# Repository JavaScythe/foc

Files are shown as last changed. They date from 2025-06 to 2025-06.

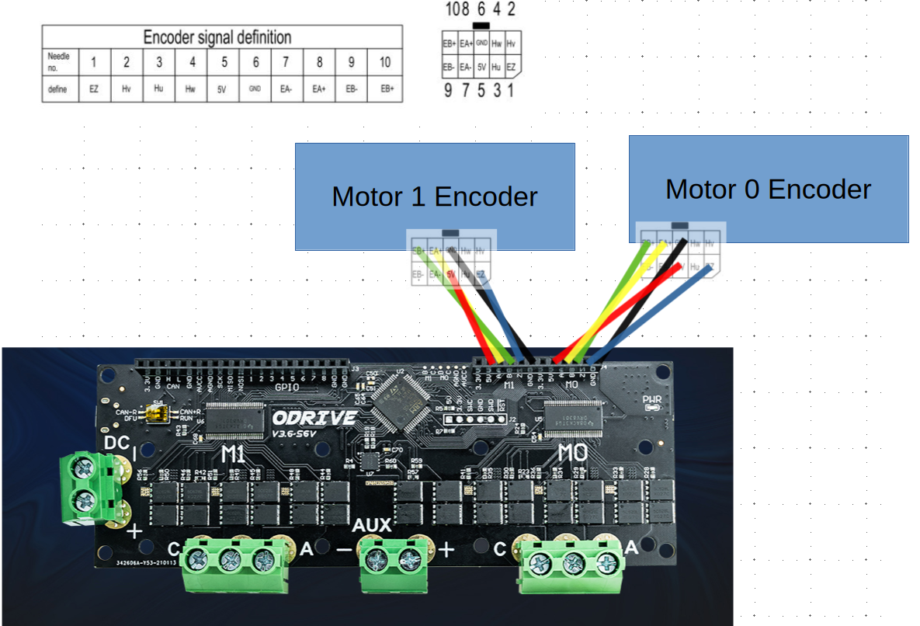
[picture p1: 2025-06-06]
motorencoderwiringguide.png

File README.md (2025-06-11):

# foc
Hyper realistic two-channel sim racing seatbelt tensioner with two 48V 54+54A FOC motors and controller that blows commercial 1300$ solutions out of the water

Specifically, it is high torque low latency that comes with its own software with support for real dynamic frequency effects for haptic feedback

### PLEASE see [JOURNAL.md](JOURNAL.md)

### Why?
- HackClub's great initiative [highway](https://highway.hackclub.com): not just "free money" but a nice community of beginners and advanced that help each other
- Lack of respect for realism in sim racing: All too often "immersion" devices are just smoke and mirrors to generate profit, lacking careful design for realism, and the community defends this.
- Vastly overpriced consumer solutions: Really? 1300$ for something that can be surpassed by a consumer with 350$?
- Fun but complex to build toy: Using the rig is fun, but building stuff for it is better

### Pictures









### BOM
|Name |Quantity|Price Total  |Link  |
|---|---|---|---|
|ODrive3.6 56V|1|60$ |alibaba.com/product-detail/ODrive3-6-FOC-BLDC-Servo-Dual_1601406724288.html|
|S70BL146-430|2|120$|alibaba.com/product-detail/S70BL146-430-Brushless-Dc-Motor-High_1600943342358.html|
|4 Point Belt|1|19$|aliexpress.us/item/3256807037196658.html|
|2kw 40A 48V PSU|1|100$|alibaba.com/product-detail/High-Quality-2000W-48V-41-6A_1600901714728.html|
|SimHub License+Motion License|1|45€|simhubdash.com/simhub-motion-addon-licence/|

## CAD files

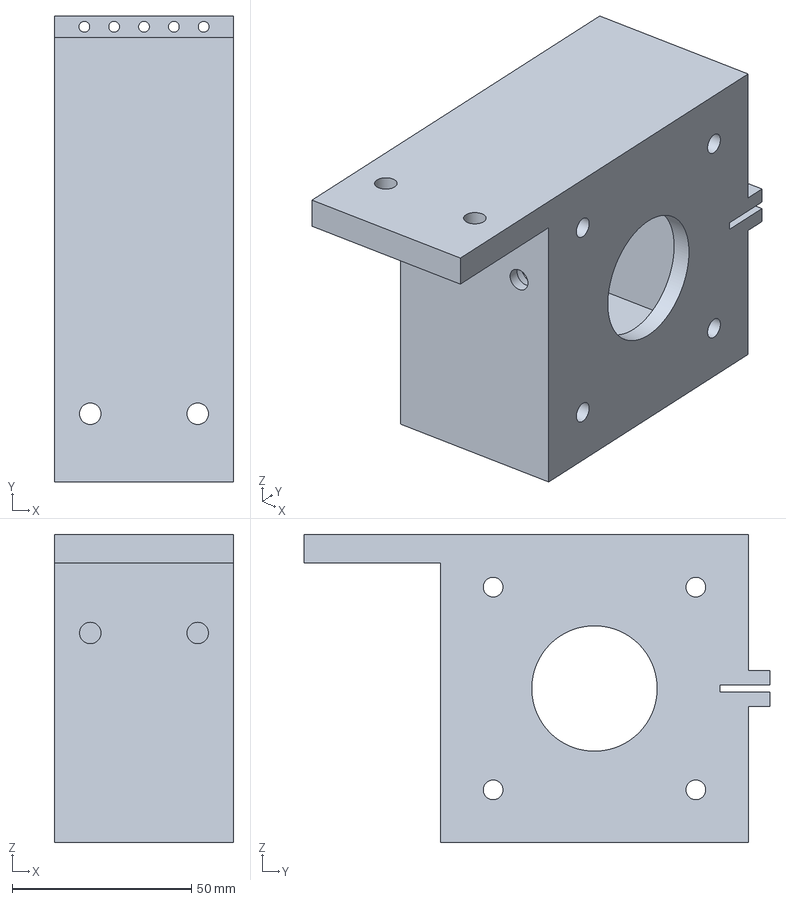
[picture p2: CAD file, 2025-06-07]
cad/realmountstrong.3mf
50.0 x 130.1 x 86.0 mm

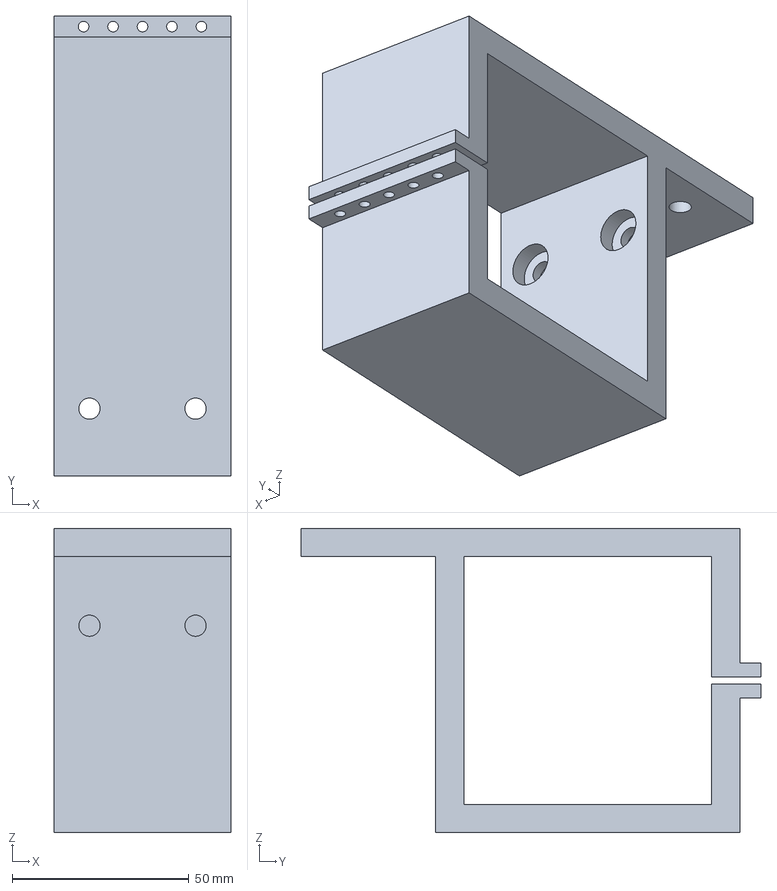
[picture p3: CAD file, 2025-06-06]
suppmount.FCStd
50.0 x 130.1 x 86.0 mm

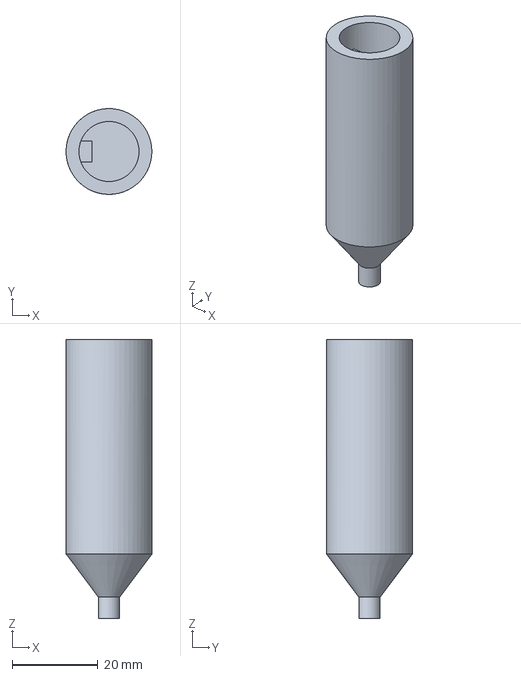
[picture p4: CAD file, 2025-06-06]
axis.FCStd
20.0 x 20.0 x 65.0 mm

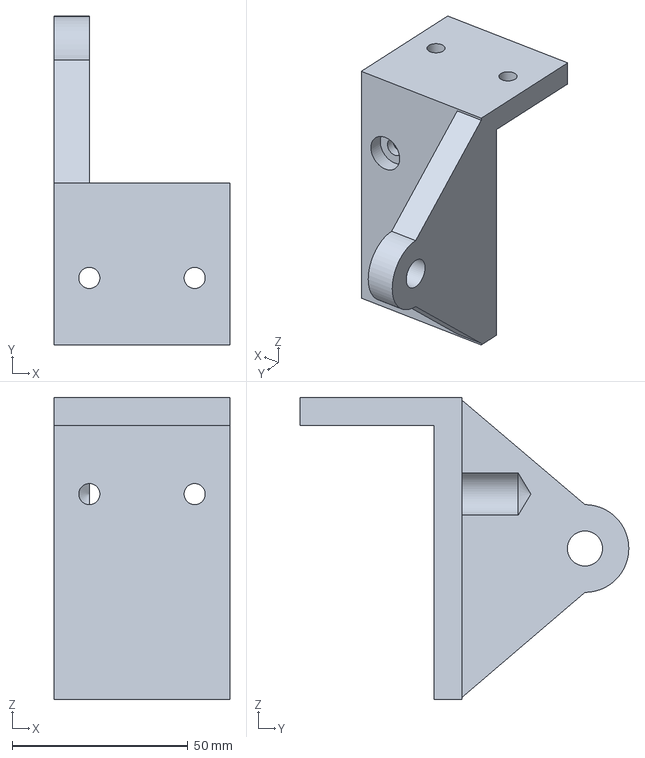
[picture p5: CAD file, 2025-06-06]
axleholder.FCStd
50.0 x 93.6 x 86.0 mm

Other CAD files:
testingassembly.FCStd
cad/axis.3mf
cad/axleholder.3mf
cad/suppmount.3mf

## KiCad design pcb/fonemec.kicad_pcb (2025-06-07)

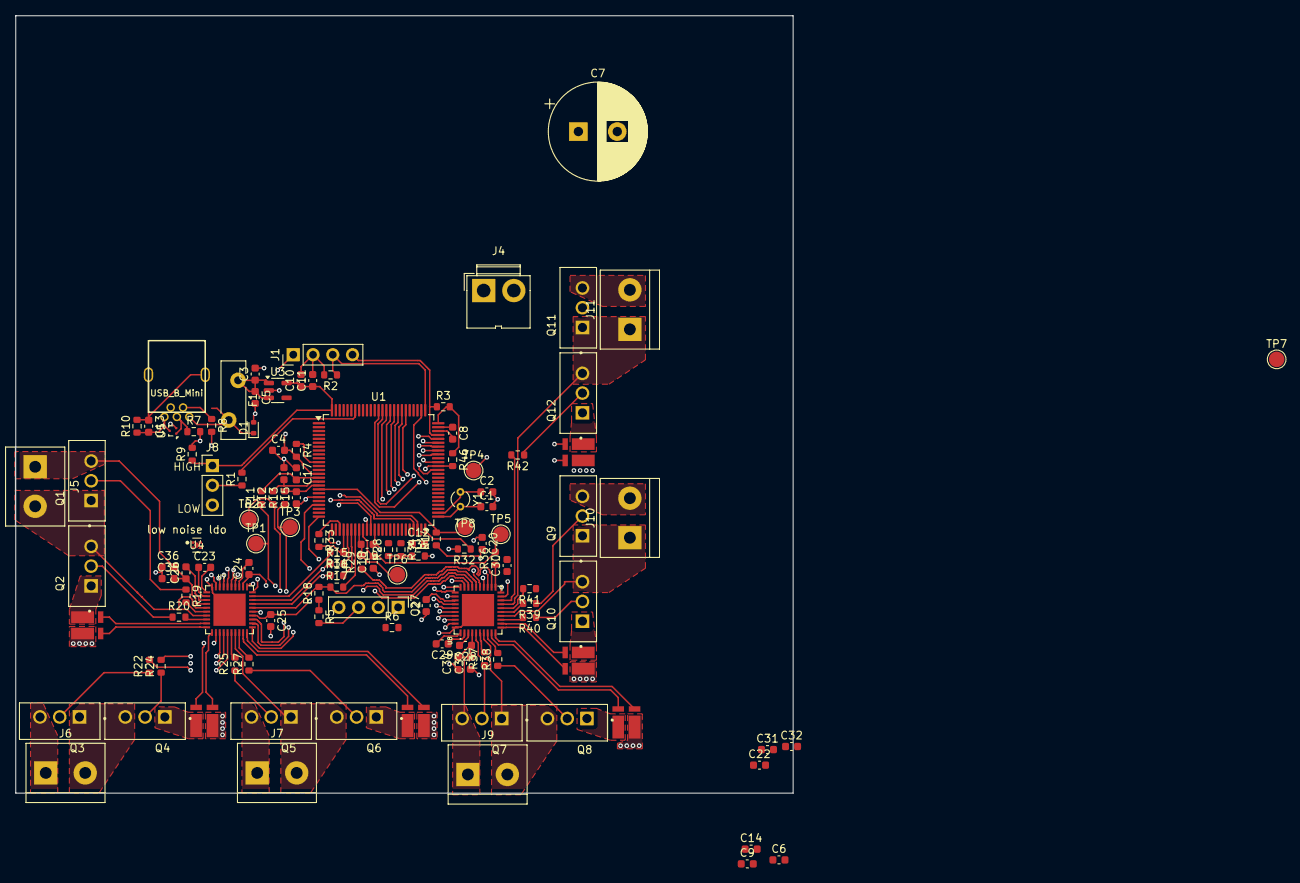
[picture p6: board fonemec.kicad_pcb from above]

Board: 4 copper layers, 100.0 x 100.0 mm, 120 parts (0 on the bottom side), 122 nets.

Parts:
C1, C2: 22pF; C_0603_1608Metric
C3, C5, C8, C12: 10 µF X7R; C_0603_1608Metric
C4: 0.1uF; C_0603_1608Metric
C6, C10: 10 0nF; C_0603_1608Metric
C7: Low-ESR polymer electrolytic 470uF 63V; CP_Radial_D12.5mm_P5.00mm
C9, C11: 1 µF; C_0603_1608Metric
C13: 1 nF; C_0603_1608Metric
C14, C22, C33, C36: 22uf Ceramic MLCC X7R; C_0603_1608Metric
C15, C16, C17, C18, C19, C20: 1nF; C_0603_1608Metric
C23, C29: X7R 47nF >48V; C_0603_1608Metric
C24, C27: X7R 1uF 6.3V; C_0603_1608Metric
C25, C30: X7R 0.1uF 6.3V; C_0603_1608Metric
C26, C28: X7R 1uF 16V; C_0603_1608Metric
C31: X7R 22uF >63V; C_0603_1608Metric
C32: X7R 0.1uF >63V; C_0603_1608Metric
C34, C35: 0.1uf Ceramic MLCC X7R; C_0603_1608Metric
D1: PESD5V0S1BA; D_SOD-523
F1: ASMD050-2; Fuse_Bourns_MF-RG400
J1: 01x04 SWD; PinHeader_1x04_P2.54mm_Vertical
J2: 01x04 USART; PinHeader_1x04_P2.54mm_Vertical
J3: USB_B_Mini; USB-Mini-B_2leg
J4: 01x02 48V; JWT_A3963_1x02_P3.96mm_Vertical
J5: Motor 1 Phase A; TerminalBlock_bornier-2_P5.08mm
J6: Motor 1 Phase B; TerminalBlock_bornier-2_P5.08mm
J7: Motor 1 Phase C; TerminalBlock_bornier-2_P5.08mm
J8: Conn_01x03_Pin; PinHeader_1x03_P2.54mm_Vertical
J9: Motor 2 Phase A; TerminalBlock_bornier-2_P5.08mm
J10: Motor 2 Phase B; TerminalBlock_bornier-2_P5.08mm
J11: Motor 2 Phase C; TerminalBlock_bornier-2_P5.08mm
Q1, Q2, Q3, Q4, Q5, Q6, Q7, Q8, Q9, Q10, Q11, Q12: CSD19536KCS; TO254P1036X470X1965-3
R1, R2, R3, R4, R5: 100K; R_0603_1608Metric
R6: 1K; R_0603_1608Metric
R7, R8, R15, R16, R17, R28, R31, R35: 22; R_0603_1608Metric
R9: 1.5K; R_0603_1608Metric
R10: 1M; R_0603_1608Metric
R11, R12, R13, R14, R29, R36: 100; R_0603_1608Metric
R18, R32, R33, R34, R46: 10K; R_0603_1608Metric
R19, R20, R22, R24, R25, R27, R37, R38, R39, R40, R41, R42: 2; R_0603_1608Metric
R21, R23, R26, R43, R44, R45: R_Shunt; RES_WSK12161L000FEA
TP1: TP1SOA; TestPoint_Pad_D2.0mm
TP2: TP1SOB; TestPoint_Pad_D2.0mm
TP3: TP1SOC; TestPoint_Pad_D2.0mm
TP4, TP7: TPGND; TestPoint_Pad_D2.0mm
TP5: TP2SOC; TestPoint_Pad_D2.0mm
TP6: TP2SOB; TestPoint_Pad_D2.0mm
TP8: TP2SOA; TestPoint_Pad_D2.0mm
U1: STM32F405VGTx; LQFP-100_14x14mm_P0.5mm
U3: AP2112K-3.3; SOT-23-5
U4: PTPS7A0218PDQNR; DQN0004A-MFG
U5: TPD2EUSB30; Texas_DRT-3
U7, U8: DRV8323SRTAT; QFN50P600X600X80-41N415X415
Y1: 8Mhz; Crystal_DS26_D2.0mm_L6.0mm_Vertical

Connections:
1CAL: U1.65 (PC8), U7.31 (CAL)
1ENABLE: U1.63 (PC6), U7.30 (ENABLE)
1GHA: R19.2, U7.6 (GHA)
1GHB: R22.2, U7.15 (GHB)
1GHC: R25.2, U7.16 (GHC)
1GLA: R20.2, U7.8 (GLA)
1GLB: R24.2, U7.13 (GLB)
1GLC: R27.2, U7.18 (GLC)
1INHA: U1.67 (PA8), U7.34 (INHA)
1INHB: U1.69 (PA10), U7.36 (INHB)
1INHC: U1.48 (PB11), U7.38 (INHC)
1INLA: U1.68 (PA9), U7.35 (INLA)
1INLB: U1.36 (PB1), U7.37 (INLB)
1INLC: U1.47 (PB10), U7.39 (INLC)
1NFAULT: R46.2, U1.64 (PC7), U7.25 (NFAULT)
1SAN: R21.2, U7.10 (SNA)
1SAP: R21.3, U7.9 (SPA)
1SBN: R23.2, U7.11 (SNB)
1SBP: R23.3, U7.12 (SPB)
1SCN: R26.2, U7.20 (SNC)
1SCP: R26.3, U7.19 (SPC)
1SHA: J5.2, Q1.1 (S), Q2.5 (D), U7.5 (VDRAIN), U7.7 (SHA)
1SHB: J6.2, Q3.1 (S), Q4.5 (D), U7.14 (SHB)
1SHC: J7.2, Q5.1 (S), Q6.5 (D), U7.17 (SHC)
1SOA: C17.2, R11.2, U1.15 (PC0)
1SOB: C16.2, R12.2, U1.16 (PC1)
1SOC: C15.2, R13.2, U1.17 (PC2)
2CAL: U1.88 (PD7), U8.31 (CAL)
2ENABLE: U1.87 (PD6), U8.30 (ENABLE)
2GHA: R37.2, U8.6 (GHA)
2GHB: R39.2, U8.15 (GHB)
2GHC: R41.2, U8.16 (GHC)
2GLA: R38.2, U8.8 (GLA)
2GLB: R40.2, U8.13 (GLB)
2GLC: R42.2, U8.18 (GLC)
2INHA: U1.81 (PD0), U8.34 (INHA)
2INHB: U1.83 (PD2), U8.36 (INHB)
2INHC: U1.85 (PD4), U8.38 (INHC)
2INLA: U1.82 (PD1), U8.35 (INLA)
2INLB: U1.84 (PD3), U8.37 (INLB)
2INLC: U1.86 (PD5), U8.39 (INLC)
2NFAULT: R32.2, U1.77 (PA15), U8.25 (NFAULT)
2SAN: R43.2, U8.10 (SNA)
2SAP: R43.3, U8.9 (SPA)
2SBN: R44.2, U8.11 (SNB)
2SBP: R44.3, U8.12 (SPB)
2SCN: R45.2, U8.20 (SNC)
2SCP: R45.3, U8.19 (SPC)
2SHA: J9.2, Q7.1 (S), Q8.5 (D), U8.5 (VDRAIN), U8.7 (SHA)
2SHB: J10.1, Q9.1 (S), Q10.5 (D), U8.14 (SHB)
2SHC: J11.1, Q11.1 (S), Q12.5 (D), U8.17 (SHC)
2SOA: R14.2, TP8.1, U1.18 (PC3)
2SOB: C19.2, R29.2, TP6.1, U1.33 (PC4)
2SOC: C18.2, R36.2, TP5.1, U1.34 (PC5)
+5V: C3.1, C5.1, F1.1, U3.1 (VIN), U3.3 (EN), U4.3 (EN), U4.4 (IN)
AGND: C24.1, C25.2, C27.1, C30.2, U7.32 (AGND), U8.32 (AGND)
GND: C1.2, C2.2, C3.2, C4.1, C5.2, C6.2, C7.1, C8.1, C9.2, C10.2, C11.2, C12.1, C13.2, C14.1, C15.1, C16.1, C17.1, C18.1, C19.1, C20.1, C22.1, C31.1, C32.1, C33.1, C34.1, C35.1, C36.1, D1.2 (A), J1.2, J2.2, J3.5 (GND), J4.1, J8.3, R2.2, R10.1, R21.1, R23.1, R26.1, R43.1, R44.1, R45.1, TP4.1, TP7.1, U1.10 (VSS), U1.20 (VSSA), U1.27 (VSS), U1.37 (PB2), U1.74 (VSS), U1.99 (VSS), U3.2 (GND), U4.2 (GND), U5.3 (GND), U7.40 (PGND), U7.41 (EXP), U8.40 (PGND), U8.41 (EXP)
NRST: C4.2, J1.1, R4.2, U1.14 (NRST)
unnamed: C31.2, C32.2
unnamed: D1.1 (K), F1.2, J3.1 (VBUS)
unnamed: J1.3, R2.1, U1.76 (PA14)
unnamed: J1.4, R3.1, U1.72 (PA13)
unnamed: J2.1, R6.2
unnamed: J3.3 (D+), R7.1, U5.1 (D+)
unnamed: J3.2 (D-), R8.1, U5.2 (D-)
unnamed: C13.1, J3.6 (Shield), R10.2
unnamed: J8.2, R1.1
unnamed: Q1.4 (G), R19.1
unnamed: Q2.4 (G), R20.1
unnamed: Q2.1 (S), R21.4
unnamed: Q3.4 (G), R22.1
unnamed: Q4.4 (G), R24.1
unnamed: Q4.1 (S), R23.4
unnamed: Q5.4 (G), R25.1
unnamed: Q6.4 (G), R27.1
unnamed: Q6.1 (S), R26.4
unnamed: Q7.4 (G), R37.1
unnamed: Q8.4 (G), R38.1
unnamed: Q8.1 (S), R43.4
unnamed: Q9.4 (G), R39.1
unnamed: Q10.4 (G), R40.1
unnamed: Q10.1 (S), R44.4
unnamed: Q11.4 (G), R41.1
unnamed: Q12.4 (G), R42.1
unnamed: Q12.1 (S), R45.4
unnamed: R1.2, U1.94 (BOOT0)
unnamed: R15.2, U1.30 (PA5)
unnamed: R16.2, U1.31 (PA6)
unnamed: R17.2, U1.32 (PA7)
unnamed: R28.2, U1.35 (PB0)
unnamed: C1.1, U1.51 (PB12), Y1.2
unnamed: C2.1, U1.52 (PB13), Y1.1
unnamed: C12.2, U1.49 (VCAP_1)
unnamed: C8.2, U1.73 (VCAP_2)
unnamed: C23.1, U7.2 (CPH)
unnamed: C23.2, U7.1 (CPL)
unnamed: C24.2, U7.33 (DVDD)
unnamed: R31.2, U7.29 (NSCS)
unnamed: R11.1, TP1.1, U7.23 (SOA)
unnamed: R12.1, TP2.1, U7.22 (SOB)
unnamed: R13.1, TP3.1, U7.21 (SOC)
unnamed: C26.2, U7.3 (VCP)
unnamed: C29.1, U8.2 (CPH)
unnamed: C29.2, U8.1 (CPL)
unnamed: C27.2, U8.33 (DVDD)
unnamed: R35.2, U8.29 (NSCS)
unnamed: C20.2, R14.1, U8.23 (SOA)
unnamed: R29.1, U8.22 (SOB)
unnamed: R36.1, U8.21 (SOC)
unnamed: C28.2, U8.3 (VCP)
SPI_MISO: R16.1, U7.27 (SDI), U8.27 (SDI)
SPI_MOSI: R17.1, R18.2, U7.26 (SDO), U8.26 (SDO)
SPI_NSCS_1: R31.1, R33.2, U1.29 (PA4)
SPI_NSCS_2: R28.1, R34.2, R35.1
SPI_SCK: R15.1, U7.28 (SCLK), U8.28 (SCLK)
USB D+: R7.2, R9.2, U1.71 (PA12)
USB D-: R8.2, U1.70 (PA11)
USRX: J2.3, R5.2, U1.26 (PA3)
USTX: J2.4, U1.25 (PA2)
VDD: C10.1, C11.1, J8.1, R3.2, R4.1, R5.1, R6.1, R9.1, R18.1, R32.1, R33.1, R34.1, R46.1, U1.11 (VDD), U1.19 (VDD), U1.28 (VDD), U1.50 (VDD), U1.75 (VDD), U1.100 (VDD), U3.5 (VOUT)
VDDA: C6.1, C9.1, C25.1, C30.1, U1.22 (VDDA), U4.1 (OUT), U7.24 (VREF), U8.24 (VREF)
VM: C7.2, C14.2, C22.2, C26.1, C28.1, C33.2, C34.2, C35.2, C36.2, J4.2, J5.1, J6.1, J7.1, J9.1, J10.2, J11.2, Q1.5 (D), Q3.5 (D), Q5.5 (D), Q7.5 (D), Q9.5 (D), Q11.5 (D), U7.4 (VM), U8.4 (VM)

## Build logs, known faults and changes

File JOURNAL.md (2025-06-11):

124 Hours total

### 5-14-25: Highway announced
### 5-18-25: Idea Inception

After exploring highway and seeing what was possible, I immediately thought of projects for my sim racing rig. Initially I thought of motion via actuators. After a bit of browsing, it was clear this was outside the possible grant size. I did find seatbelt tensioners which I had previously not considered because of the cost.

2 Hours

### 5-19-25: Seatbelt tensioner idea

After thinking a little more, I researched a few existing solutions and tried to determine what kind of motors/power they were using.

I sent a few messages to different vendor's supports, and got a range of responses:


The first is from MotionSystems.eu, obviously using chatgpt or something. Embarassing for them, considering they then followed up with a 2nd message removing the [replace... part and then a 3rd where they finally removed the X cm.

SimStix.com also appealed to bandwagon saying everyone else is fine with it (a common sentiment for technical specifications in simracing—but that's a different argument). No helpful information



Qubic themselves, despite emphaizing my feedback's importance to them, did not even respond. This project is therefore dedicated to dragging your sorry overpriced weak belt tugging system through the mud.

The most I got from anyone was on the r/simracing discord, who suggested a BLDC motor.

The Qubic's BT1 does list an operating wattage which makes it easy to determine the maximum wattage for each motor inside: far less than expected.

10 Hours

### 5-20-25: Motor search 1
With this lack of new knowlege, I set out to find what technology or type of motor would even allow for high speed torque. After much research and covering things like AC Servos to plantary gearbox combinations to even linear actuators, it was clear that PSMS and BLDC were what I was looking for, because it was the same as the haptic capable direct drive wheels. Now, finding one with sufficient torque and speed, as well as magnitude. A tensioner like this would operate nearly always at stall, which is terrible for most motors.

This is one provided for a popular DIY seatbelt tensioner example. Not good at all for this purpose.

5 Hours

### 5-21-25: Motor Search 2
Armed with this new knowlege, I combed aliexpress for suitible motors. I found a great, cheap pair with controllers included. I considered the motor search done, but when I went to double check, I found the motors were actually hybrid servo steppers, not capable of the operation I was looking for. However, as tragic as it was to find that my research and searching had led to nothing, it introduced me to FOC and torque control mode for motors.

7 Hours

### 5-22-25: Specification Development
After reviewing what I did know about existing solution: BLDC and wattage, and specifically, the force/tempature/time graph listed on BT1's page. It basically explained that the high the force applied over a longer time, the unit would heat it, eventually past safe limits and have to turn down power. It did so in a cryptic fashion that the average consumer cannot read, and made the cases where little force was applied and thus could sustain forever, were a huge win and not a basic expectation. Another point against QS. 


This however solidifed my idea for the sustained holding torque of the motor. 1.2-1.5Nm holding, which means about 2.5 peak. This would put it far above the BT1. Where the BT1 claims maximum of 200N (using unknown internal spool radius, I suspect a very small and thus slower accelerating), I can claim 250Nm with a spool of 1cm (which for low interia application like this means insane acceleration).

7 Hours

### 5-23-25: Motor Search 3 and Specification Development
Now knowing exactly what I was looking for, I was hit with yet another obstacle: I couldn't find it on aliexpress. Well, there were definetly correct technology motors, but none rated for the torque I required, for a anywhere reasonable price. I turned instead to alibaba, which due to its difficult search system, yielded little results. This was a all day affair and did nothing but rule out model names.

5 Hours

### 5-24-25: Motor Search 4
Finally I narrowed the list down by going to manufacture websites and looking through their collection.



Then, I found one for about the same price (60$) that was very good. With 2Nm holding torque, and a whopping 6Nm peak torque, this thing could tear BT1 to pieces. With a spool of 1cm, 6Nm means an insane (and unsafe) 600N of force (mostly down because I am tall in comparison for the seat). This is too much for this application, but the capability to do so means it can run regular 0-200N without breaking a sweat (literally. being in Florida, another thermal energy producing object (twice) is not a welcome proposition)

6 Hours

### 5-25-25 Research and Controller Build 1
An important and critical part of FOC control is the controller itself. It has to control each phase's high and low FET, and in this case two motors, for a total of 12 MOSFETs.

I spent most of this day heavily immersed in learning about FOC control and the hardware compontents that allow it to function. This was both difficult and rewarding.

Additionally, the high power required to drive these motors means the controllers will have to withstand a lot of current. Thus began the design and selection of ICs for the controller PCB. I browsed and browsed and came up with the STM32F405 as MCU for its many PWM for gate control and ADCs for current sense. I ran out of time to select a driver IC and slept.

6 Hours

### 5-26-25 Controller Build 2
I selected the DRV8323RS (remember the R) because I planned to use VESC firmware. Here is a summary of the choices determined today:
MCU: STMF405VGT, chosen for compatibilty with VESC firmware and high GPIO count, ADC for current sense
Motor driver: 2x DRV8323S, no internal buck. High power LDO and additonal low noise LDO both already implemented. DRV8323S compatible with VESC via SPI, and internal current sense amplifiers

Browsing LSCS's collection to find applicable

MOFSET: 12x CSD19536KCS, high voltage, low RDS on, big thermally conductive package. Two for each phase: 2x3x2
6x Shunt resistors: Opting for higher quality control for the basis of FOC control: torque control by current measurement. One for each phase instead of Kirchoff's rule estimation for last one. In lower rpm scenarios like this one, two would be a noticable downgrade.
Connections: USART, SWD, and USB all made avaliable and connected for debugging

5 Hours

### 5-27-25 Controller Build 3
This was the actual start to the PCB. Opening KiCad 9, making project, and placing the STM32 (already in library for once). Addtionally, I set up Syncthing so I could work on it from my windows computer as well, which worked perfectly. With a billion tabs open in documentation, by the end of the day, things were placed:


7 Hours

### 5-28-25 Controller Build 4
Continuing on the build, I added the actual gates and connections with those. This took a while because I initially did it wrong. Also added the two LDOs.


8 Hours

### 5-29-25 Controller Build 5
Second gate, connect gate drivers. Checking and check again with manufacture docs. Not much to reflect on, complex work.


8 Hours (Day off from testing...)

### 5-30-25 to 5-31-25 to 6-1-25 Controller Layout
Some parts picked (caps, crystal, etc), then a long time spent reading PCB design docs for EMI. Since this is both high amp, high volatage, and very sensitive current sense lines. A true reciepe for EMI disaster.

I started on the layout on a plane flight (and continued it over the next two, which took 3 days. Perfect time to rot on KiCad)


The mountain to climb

Drive 1 done

Getting there

The ground fills

18 Hours

### 6-2-25 Turn Around
At this point I tried to estimate the cost of making this PCB by uploading some gerbers and setting the board. Even without PCBA, the PCB and parts came out to way more than 100$, and in best cases just 70-80$. This is when I realized that purchasing an existing controller would be cheaper. I spent some time looking for alternatives and came up with the following:

Of the existing solutions, the Odrive 3.6 stood out for meeting the requirements.

Unfortunately, it only has two shunt resistors where I would have prefered the full three. In theory the third's current can be calculated via kirchhoff's law but I'm not sure how much the inaccuracies will affect performance/smoothness.

This is also avaliable on Alibaba for far less than any other controller of its class: 40$ (alibaba)

### 6-3-25 Case Design
Now came what I had though to be the "easy" part. While robust and powerful, these motors are not designed to withstand axial force (like that generated by the seatbelt resistance). In order to midigate this wear on the motors, and to mount them to the rig in the first place, a appropriate casing was designed.

I had to install freecad and dependecies from the arch linux archive manually over sub MB DSL. This was fun by itself, but especially adding FEM capabilites packages.

This is the face of the motor as supplied by manuf.

Here is the slot for the motor to connect to. Hopefully this will survive, if not, ABS is avaliable.

FEM for axle holder. Less than a milimeter displacement, but less than ideal. Will update perhaps.

The flexy things. I've seen/used them on other builds and its always better to be able to adjust that last few mm rather than press fit.

Some new mounting holes for the odrive.

Again not ideally, my 8020 rig has semiflat bottom profile, so only the top facing rail and the upper-most and bottom-most side rails are usable for mounting. I don't think expanding the mounts to the bottom one is necessary (the profile is quite tall).



6 Hours

### 6-4-25 Control Software
Now with this overengineered hardware, a complementary control system is required.

I spent a lot of time researching how Odrive can recieves control as well as what methods SimHub outputs to.

The telemetry aggregator/effect generator will be SimHub (License will be needed to drive motion as well as 60fps)

While most DIY solutions use Arduinos with Simhub provided sketches, this adds unnessary complexity and latency. The most efficient solution is have the PC communicate directly to the on-board STM32F405.

Simhub, however, doesn't support this out of the box. (It does support custom serial devices, and so does ODrive. This means that plug-n-play would technically work, but Odrive's ASCII protocol is human readable text based, which is unnessary overhead and adds massive latency.)

Additionally, controlling ODrive native protocol from simhub's custom serial is impossible, since computing dynamic CRC and sequence number is not possible in SimHub command editor.

6 Hours

### 6-5-25 Control Software 2
After reading many many pages of documentation and asking a question in discord (which was answered very promptly and kindly by simhub's developer—big shout out to him), the solution was clear: UDP output to script to convert to Odrive native USB.

Thus begins the development of `han.c`
han.c design choices
- Asncy USB for minimal latency-
- 1KHz control loop for rumble effects
- 2x (expandable) rumble effect combine
- Debug mode for latency debugging
- Precalculated CRC8/16 for Odrive native spec 

In order to make full use of this hardware, road rumble (or other frequency effects) can also be implemented. In SimHub, the UDP output will be configured for N+2 axis, Torque right, Torque left, effect*n.

Then, mimicing simhub's own bassshaker driver method, frequency for each effect is determined by its amplitude. The script does this calculation per frame and drives the motor at this frequency and amplitude.


A lot of C (not my favorite language, but oh so fast) writing.

Currently there can be up to 1ms where a new torque is recieved and when it is implemented. This will probably not matter.

This still uses the ODrive's CDC interface, which by default runs the ASCII protocol. This must be disabled by Odrive config

8 Hours

### 6-6-25 Calibration
The Odrive has to be set up and configured in the correct mode, in addtion to normal BLDC calibration

The motor has a built in differential quadrature encoder with index (as well as hall effects, but those will not be used)


I spent time writing the calibration file to do the manual steps automatically and set the torque mode, as well as the CDC protocol mode.

The calibration file (calib.py) only has to be run once, then at start up it will find the index position (in direction of tensioning seatbelt)

It also disables many safety features like torque mode velocity limits, velocity limits, and acceleration limits. If you fix NONE of these, at least fix torque mode velocity limit, because if the belt breaks and the motor is free to apply torque without resistance, it will speed up to its full power very quickly, swinging whatever belt remains on its axis at maximum speed.

E-stop: Such a vivacious design requires a safety feature. A button to pull nRST on the Odrive will stop the motor torque and restart the driver.

7 Hours

### 6-7-25 Case Revisited
After reviewing the motor specifications again, I began to worry about the sheet power this thing could output, so I ran some FEM simulations to see if the mounts would even hold.

Here is 100N on each holding screw to simulate the twisting motor (Not accurate but whatever) 

With the additional part to span the profile:

With additional support, should have done that in the first place

New final case design (remember, it will be mirrored and printed 2x)


Now I wrote up a bunch of stuff, embellished the journal, and started the submittal process.

3 Hours

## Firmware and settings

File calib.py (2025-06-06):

import odrive
from odrive.enums import *
import time

print("Finding ODrive...")
odrv0 = odrive.find_any()
print("Connected.")

omotor = odrv0.axis0

print("Configuring motor...")
omotor.motor.config.pole_pairs = 4
omotor.motor.config.current_lim = 58
omotor.motor.config.calibration_current = 15
omotor.motor.config.torque_constant = 0.12 
omotor.motor.config.pre_calibrated = False

print("Configuring encoder...")
omotor.encoder.config.mode = ENCODER_MODE_INCREMENTAL
omotor.encoder.config.cpr = 8192 # Change
omotor.encoder.config.use_index = True
omotor.encoder.config.pre_calibrated = False

omotor.config.startup_motor_calibration = False

omotor.config.startup_encoder_index_search = True
omotor.encoder.config.index_search_unidirectional = True
omotor.encoder.config.calib_scan_distance = 8192 # Change to 2-3x CPR
print("Configuring autoindex for SPECIFIC DIRECTION, double check");
omotor.config.calibration_lockin.vel = +1

omotor.config.startup_encoder_offset_calibration = False
omotor.config.startup_closed_loop_control = True

print("Running full calibration sequence...")
omotor.requested_state = AXIS_STATE_FULL_CALIBRATION_SEQUENCE
while omotor.current_state != AXIS_STATE_IDLE:
    time.sleep(0.1)
print("Calibration complete.")

omotor.motor.config.pre_calibrated = True
omotor.encoder.config.pre_calibrated = True

print("Setting torque control mode...")
omotor.controller.config.control_mode = CONTROL_MODE_TORQUE_CONTROL
omotor.controller.config.input_mode = INPUT_MODE_PASSTHROUGH

# safety
omotor.controller.enable_torque_mode_vel_limit = False
omotor.controller.config.vel_limit = 10000
omotor.trap_traj.config.accel_limit = 10000
omotor.trap_traj.config.decel_limit = 10000

print("Running index search...")
omotor.requested_state = AXIS_STATE_ENCODER_INDEX_SEARCH
while omotor.current_state != AXIS_STATE_IDLE:
    time.sleep(0.1)

print("Running encoder offset calibration...")
omotor.requested_state = AXIS_STATE_ENCODER_OFFSET_CALIBRATION
while omotor.current_state != AXIS_STATE_IDLE:
    time.sleep(0.1)

print("Entering closed-loop control...")
omotor.requested_state = AXIS_STATE_CLOSED_LOOP_CONTROL

print("Applying test torque...")
for i in range(3):
    omotor.controller.input_torque = 0.05  # Nm
    time.sleep(1)
    omotor.controller.input_torque = -0.05
    time.sleep(1)

omotor.controller.input_torque = 0
print("Torque test complete.")
print("Saving configuration...")
odrv0.config.usb_cdc_protocol = 0x0;
odrv0.save_configuration();
print("Done.")
